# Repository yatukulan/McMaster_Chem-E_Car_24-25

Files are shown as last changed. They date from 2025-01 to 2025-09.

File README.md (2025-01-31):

# McMaster_Chem-E_Car_24-25
The codebase for the McMaster Chem-E Car Team from 2024-2025.

This project uses an Adafruit Feather RP2040 Adalogger microcontroller programmed in the Arduino programming language. The car runs off a chemical reaction and is stopped by a chemical reaction as well. However, the code and the microcontroller are used to start the stopping reaction and stir the mixtures while monitoring it to identify when to stop based on a temperature threshold. It also uses an IMU to keep the car going straight, a servo for starting the stopping reaction, two motor drivers to run the drive motors, and two motors for stirring the reactions. The car's main drive system will be powered from a custom-built alkaline battery while the remaining auxiliary systems are powered from a smaller Li-Po battery.

The major components used are as follows:<br />
2 - N20 100 RPM Motors (for drive system)<br />
2 - N20 1000 RPM Motor (for reaction stirring mechanisms)<br />
2 - SER0039 Servo Motor (for initially mixing reactants)<br />
2 - DRV8847 Motor Drivers<br />
1 - DS18B20 Temperature Sensor (for measuring temperature of braking reaction)<br />
1 - Adafruit 9-DOF Orientation IMU Fusion Breakout (BNO085)<br /> 
1 - Adafruit Feather RP2040 Adalogger Microcontroller<br />
1 - 1200 mAh Li-Po Battery<br />

This repository also contains the custom-made PCB design for the component wiring we are using this year. The design was made using Altium, source files & gerber files are present in this repository.

The main objective of the competition is to design a small car to carry a certain amount of weight a set distance while powering and stopping the vehicle with a chemical reaction. The distance and weight vary each year. The compectition is hosted by the American Institute of Chemical Engineers (AIChE).

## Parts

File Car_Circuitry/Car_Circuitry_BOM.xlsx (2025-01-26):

Comment | Description | Designator | Footprint | LibRef | Quantity | Total | Boards
TPS552892RYQR | Integrated Circuit | BOOST1 | TPS552892RYQR | TPS552892RYQR | 1 | 5 | 5
TPS61023DRLT | Integrated Circuit | BOOST2 | SOTFL50P160X60-6N | TPS61023DRLT | 1 | 5
100 nF | Capacitor | C1, C2 | CAPC2012X95N | CL21B104KBCNNNC | 2 | 10
10 μF | Capacitor | C3, C4, C19 | CAPC2012X140N | CL21B106KOQNNNE | 3 | 15
82 nF | Capacitor | C5 | CAPC1005X55N | GRM155R61A823KA01D | 1 | 5
24 nF | Capacitor | C6 | CAPC2013X94N | 08051C243JAT2A | 1 | 5
4.7 μF | Capacitor | C7 | CAPC1608X80N | C1608X6S1C475K080AC | 1 | 5
56 μF | Capacitor Polarised | C8 | 16SVF82M | 20SVPF56MX | 1 | 5
22 μF | Capacitor | C9, C15, C16, C17 | CAPC3225X270N | GRM32ER61E226KE15K | 4 | 20
100 nF | Capacitor | C10, C11, C12, C18 | CAPC1005X55N | CL05B104KA5NNNC | 4 | 20
27 μF | Capacitor Polarised | C13, C14 | 16SVF82M | 25SVPF27MX | 2 | 10
22 μF | Capacitor | C20, C21 | CAPC3216X180N | CL31B226KPHNNNE | 2 | 10
SSB44-M3_5BT | Schottky Diode | D1 | DIOM5436X244N | SSB44-M3_5BT | 1 | 5
B2B-XH-A(LF)(SN) | CONN HEADER VERT 2POS 2.5MM | DRML, DRMR, PROP, SOL, STMB, STMP, SW | FP-B2B-XH-A_LF_SN-MFG | CMP-2000-05888-3 | 7 | 35
DRV8847PWPR | Integrated Circuit | DRV1, DRV2 | SOP65P640X120-17N | DRV8847PWPR | 2 | 10
4.7 μH | Inductor | L1 | INDPM6664X610N | 74439346047 | 1 | 5
1 μH | Inductor | L2 | 74438357010 | 74438357010 | 1 | 5
Feather RP2040 Adalogger | Adafruit Microcontroller | MCU | 2796 | 2796 | 1 | 5
DMN6075S-7 | MOSFET (N-Channel) | Q1 | SOT96P240X110-3N | DMN6075SQ-7 | 1 | 5
110 mΩ | Resistor | R1, R4 | ERJ6_B_BW_R_LW_CW_D | ERJ-6DSFR11V | 2 | 10
680 mΩ | Resistor | R2, R5 | ERJ6_B_BW_R_LW_CW_D | ERJ-6DQJR68V | 2 | 10
10 kΩ | Resistor | R3, R6, R10 | RESC2012X70N | ERJ-6GEYJ103V | 3 | 15
4.7 kΩ | Resistor | R7 | RESAD1530W60L610D230 | CF1_4C472J | 1 | 5
301 Ω | Resistor | R8 | RESC1005X40N | CRCW0402301RFKED | 1 | 5
49.9 kΩ | Resistor | R9 | ERJ2RKD1004X | ERJ-2RKF4992X | 1 | 5
100 kΩ | Resistor | R11 | ERJ8ENF1000V | ERJ-8ENF1003V | 1 | 5
732 kΩ | Resistor | R12 | ERJ8ENF1000V | ERJ-8ENF7323V | 1 | 5
B3B-XH-A(LF)(SN) | CONN HEADER VERT 3POS 2.5MM | SVOB, SVOP, TMP | FP-B3B-XH-A_LF_SN-MFG | CMP-17439-000014-3 | 3 | 15

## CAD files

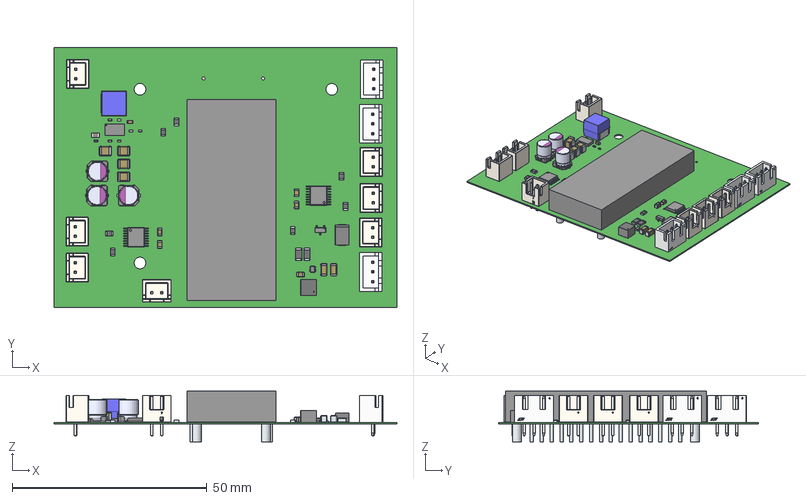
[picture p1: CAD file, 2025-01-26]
Car_Circuitry/Car_Circuitry.step
88.1 x 66.9 x 13.1 mm
solidBody x 10
Terminal x 10
solidTop x 10
FilletPin1 x 2
FilletPin2 x 2
B2B-XH-A x 7
JST Logo adjustable x 7
PinsArrayL
FilletPinR
Pins x 3
Marking x 3
JST Logo x 3
body_SSMC_4030
land_pattern_SSMC_4020 x 2
R7
Leads x 32
PinsArrayLR x 2
ThermalPad x 2
BODY-SOT
PIN1-ID

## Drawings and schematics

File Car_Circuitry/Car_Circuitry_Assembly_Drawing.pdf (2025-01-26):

1

16

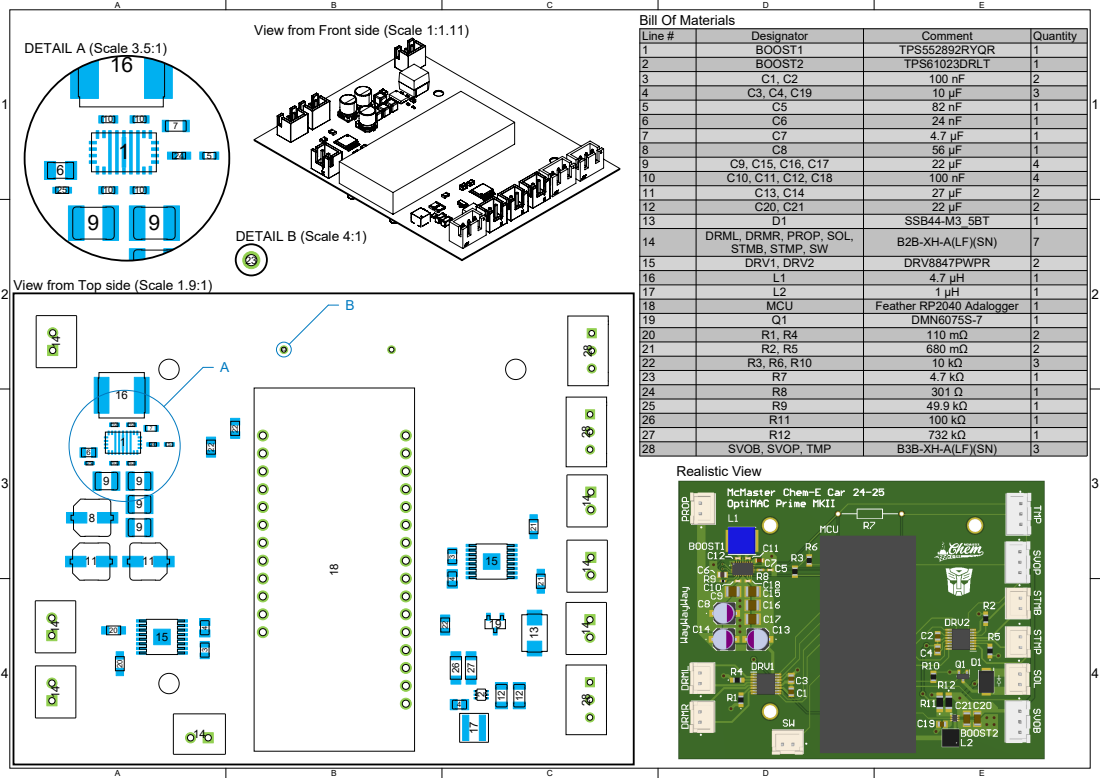
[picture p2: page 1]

View from Front side (Scale 1:1.11)

Line # | Designator | Comment | Quantity
1 | BOOST1 | TPS552892RYQR | 1
2 | BOOST2 | TPS61023DRLT | 1
3 | C1, C2 | 100 nF | 2
4 | C3, C4, C19 | 10 μF | 3
5 | C5 | 82 nF | 1
6 | C6 | 24 nF | 1
7 | C7 | 4.7 μF | 1
8 | C8 | 56 μF | | 1
9 | C9, C15, C16, C17 | 22 μF | | 4
10 | C10, C11, C12, C18 | 100 nF | | 4

12 | C20, C21 | 22 μF | 2
13 | D1 | SSB44-M3_5BT | 1
14 | DRML, DRMR, PROP, SOL, STMB, STMP, SW | B2B-XH-A(LF)(SN) | 7

15 | DRV1, DRV2 | DRV8847PWPR | 2
16 | L1 | 4.7 μH | 1
17 | L2 | 1 μH | 1
18 | MCU | Feather RP2040 Adalogger | 1
19 | Q1 | DMN6075S-7 | 1
20 | R1, R4 | 110 mΩ | 2
21 | R2, R5 | 680 mΩ | 2
22 | R3, R6, R10 | 10 kΩ | 3
23 | R7 | 4.7 kΩ | 1
24 | R8 | 301 Ω | 1
25 | R9 | 49.9 kΩ | 1
26 | R11 | 100 kΩ | 1
27 | R12 | 732 kΩ | 1
28 | SVOB, SVOP, TMP | B3B-XH-A(LF)(SN) | 3

View from Top side (Scale 1.9:1)

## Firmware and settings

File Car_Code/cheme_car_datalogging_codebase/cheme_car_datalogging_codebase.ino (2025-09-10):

// Included libraries
#include <OneWire.h>
// #include <Wire.h>
// #include <Adafruit_BNO08x.h>
#include <DallasTemperature.h>
// #include <PID_v1_bc.h>
#include <Servo.h>
#include <Adafruit_NeoPixel.h>
#include "SdFat.h"

#define NUM_PIXELS 1 // Status LED

// Add Test Fork

// Define drive motor pins
#define LEFT_PWM_1 9
#define LEFT_PWM_2 10
#define RIGHT_PWM_1 12
#define RIGHT_PWM_2 11

// Define the PWM pins for the stir bar motors
#define BRAK_STIR_PWM_1 A3
#define BRAK_STIR_PWM_2 24
#define PROP_STIR_PWM_1 6
#define PROP_STIR_PWM_2 5

// Define servo pins
#define BRAK_SERVO_PWM 13
#define PROP_SERVO_PWM 4

#define BRAK_TEMP_SENS A1 // Pin for the teperature sensor data line

// #define BNO08X_RESET -1 // No reset pin for IMU over I2C, only enabled for SPI

// #define BOOST_I2C 0x75 // This is the address when pin on converter is set to LOW

// Define chip select pin for SD card
#define SD_CS_PIN 23

// Struct for Euler Angles
// struct euler_t
// {
//   float yaw;
//   float pitch;
//   float roll;
// } ypr;

// Create servo objects
Servo brak_servo;
Servo prop_servo;

// Create BNO085 instance
// Adafruit_BNO08x bno08x(BNO08X_RESET);
// sh2_SensorValue_t sensor_value;

OneWire one_wire(BRAK_TEMP_SENS);          // Create a OneWire instance to communicate with the sensor
DallasTemperature temp_sensors(&one_wire); // Pass OneWire reference to Dallas Temperature sensor

Adafruit_NeoPixel pixel(NUM_PIXELS, PIN_NEOPIXEL, NEO_GRB + NEO_KHZ800); // Status LED

// Define files
SdFat sd;
FsFile root;
FsFile next_file;
FsFile data_file;
SdSpiConfig config(SD_CS_PIN, DEDICATED_SPI, SD_SCK_MHZ(16), &SPI1);
String file_name;

bool is_file_new = true; // Checks for new file

// The target yaw angle to keep car straight
// double goal_yaw = 0.0;

// Define IMU variables
// double yaw;            // yaw angle
// double init_yaw = 0.0; // initial yaw angle
// double yaw_diff = 0.0; // yaw angle difference

// Delta temperature
double temp_diff;

// Temperature change threshold
double temp_change;

// Initialize run count for SD card file
int run_count;

// variables to store temperature
double temperature_c; // Current temperature
double init_temp;     // Initial temperature for differential calculation

// KALMAN FILTER variables
double x_temp; // Filtered temperature
double p_temp; // Initial error covariance
// double x_IMU;  // Filtered temperature
// double p_IMU;  // Initial error covariance

// Process noise and measurement noise
double q_temp; // Process noise covariance
double r_temp; // Measurement noise covariance
// double q_IMU;  // Process noise covariance
// double r_IMU;  // Measurement noise covariance

// Keeping track of time
double curr_time = 0.0f;
unsigned long start_time;
// bool first_run = true;

const int data_size = 4; // Number of items to log
double data[data_size];  // Data array
// char data_buf[11];       // Data buffer

// PID Loop variables
// double pid_output; // The output correction from the PID algorithm

// The following numbers need to be adjusted through testing
// double k_p = 1.5;  // Proportional weighting
// double k_i = 0.03; // Integral weighting
// double k_d = 0.3;  // Derivative weighting

// Offsets & speeds for left and right wheel
// int left_offset = 0;
// int right_offset = 0;
int drive_speed = 128;
// int max_offset;

// PID control object; input, output, and goal angle are passed by pointer.
// PID car_pid(&yaw_diff, &pid_output, &goal_yaw, k_p, k_i, k_d, DIRECT);

// Buck boost converter status outputs
// bool buck_boost_short_circuit;
// bool buck_boost_overcurrent;
// bool buck_boost_overvoltage;
// String buck_boost_op_status;

// void init_buck_boost(void)
// {
//   Wire.begin(); // Begin I2C communication

//   // Change internal output voltage to 676.68 mV
//   // Change LSB
//   Wire.beginTransmission(BOOST_I2C);
//   Wire.write(0x00); // Register Address
//   Wire.write(0x5F); // Changed LSB
//   Wire.endTransmission();

//   //  Change MSB
//   Wire.beginTransmission(BOOST_I2C);
//   Wire.write(0x01); // Register Address
//   Wire.write(0x04); // Changed MSB
//   Wire.endTransmission();

//   // Disable current limiter
//   Wire.beginTransmission(BOOST_I2C);
//   Wire.write(0x02); // Register Address
//   Wire.write(0x64); // Changed LSB
//   Wire.endTransmission();

//   // Enable output
//   Wire.beginTransmission(BOOST_I2C);
//   Wire.write(0x06); // Register Address
//   Wire.write(0xA0); // Changed LSB
//   Wire.endTransmission();
// }

// String check_buck_boost_status(void)
// {
//   // Read status register
//   Wire.beginTransmission(BOOST_I2C);
//   Wire.write(0x07);
//   Wire.endTransmission(false);
//   Wire.requestFrom(BOOST_I2C, 1);

//   char status = Wire.read();

//   // Check SCP status
//   if (((status >> 7) & 0x01))
//   {
//     buck_boost_short_circuit = true;
//   }

//   // Check OCP status
//   if (((status >> 6) & 0x01))
//   {
//     buck_boost_overcurrent = true;
//   }

//   // Check OVP status
//   if (((status >> 5) & 0x01))
//   {
//     buck_boost_overvoltage = true;
//   }

//   // Check operating status
//   switch (status << 6)
//   {
//   case 0x00:
//     return "boost";
//   case 0x40:
//     return "buck";
//   case 0x80:
//     return "buck-boost";
//   case 0xC0:
//     return "reserved";
//   default:
//     return "";
//   }
// }

void drive_forward(int speed) // Drive function
{
  digitalWrite(LEFT_PWM_1, HIGH);
  digitalWrite(RIGHT_PWM_2, HIGH);
  // analogWrite(LEFT_PWM_2, speed - left_offset);
  // analogWrite(LEFT_PWM_2, speed);
  digitalWrite(LEFT_PWM_2, LOW);
  // analogWrite(RIGHT_PWM_1, speed - right_offset);
  // analogWrite(RIGHT_PWM_1, speed);
  digitalWrite(RIGHT_PWM_1, LOW);
}

void stop_driving(void) // Stop function
{
  digitalWrite(LEFT_PWM_1, HIGH);
  digitalWrite(RIGHT_PWM_2, HIGH);
  // analogWrite(LEFT_PWM_2, 255);
  digitalWrite(LEFT_PWM_2, HIGH);
  // analogWrite(RIGHT_PWM_1, 255);
  digitalWrite(RIGHT_PWM_1, HIGH);
}

void servo_dump(Servo servo, int angle_us, int delay_ms) // Dump reactants into vessel with servo
{
  // Rotate to specified position
  servo.writeMicroseconds(angle_us);
  delay(500);
  servo.writeMicroseconds(angle_us);

  delay(delay_ms); // Wait specified delay

  // Return to default position
  servo.writeMicroseconds(450);
  delay(500);
  servo.writeMicroseconds(450);
}

void start_stir(int stir_pin_1, int stir_pin_2, int speed) // Start stirring mechanism
{
  digitalWrite(stir_pin_1, LOW);  // For fast decay
  analogWrite(stir_pin_2, speed); // Set motor to speed obtained through testing
}

// void PID_loop(void) // Update motor speeds according to PID algorithm
// {
//   car_pid.Compute(); // Run compute algorithm and updates pid_output

//   if (pid_output < 0)
//   {
//     left_offset = abs(round(pid_output)); // If output needs to be adjusted in positive dir (to the right), increase left wheel speed
//     right_offset = round(pid_output);     // and decrease right wheel speed.
//   }
//   else if (pid_output > 0)
//   {
//     right_offset = abs(round(pid_output)); // If output needs to be adjusted in negative dir (to the left), increase right wheel speed
//     left_offset = -round(pid_output);      // and decrease left wheel speed.
//   }
//   else // Otherwise set both speed offsets to zero if output does not need adjustment.
//   {
//     left_offset = 0;
//     right_offset = 0;
//   }
// }

void kalman_filter(double x_k, double p_k, double q, double r, double input, bool tempTrue) // Kalman filtering algorithm
{
  // Kalman filter prediction
  double x_k_minus = x_k;     // Predicted next state estimate
  double p_k_minus = p_k + q; // Predicted error covariance for the next state

  // Kalman filter update

  /* Kalman gain: calculated based on the predicted error covariance
  and the measurement noise covariance, used to update the
  state estimate (x_k) and error covariance (p_k) */
  double k = p_k_minus / (p_k_minus + r); // Kalman gain

  // Comparison with actual sensor reading
  x_k = x_k_minus + k * (input - x_k_minus); // Updated state estimate
  p_k = (1 - k) * p_k_minus;                 // Updated error covariance

  if (tempTrue) // Update state for temperature sensor or IMU accordingly
  {
    x_temp = x_k;
    p_temp = p_k;
  }
  else
  {
    // x_IMU = x_k;
    // p_IMU = p_k;
  }
}

void printer(bool serial_true, double millis_time, double outputs[data_size]) // Output function
{
  if (serial_true) // Print data to serial or SD card file accordingly in .csv format
  {
    Serial.print(millis_time, 6);

    for (int i = 0; i < data_size; i++)
    {
      Serial.print(",");
      Serial.print(outputs[i], 6);
    }

    Serial.println("");
  }
  else
  {
    data_file.print(millis_time, 6);

    for (int i = 0; i < data_size; i++)
    {
      data_file.print(",");
      data_file.print(outputs[i], 6);
    }

    data_file.println("");
  }
}

// Enable reports for IMU
// void setReports(void)
// {
//   Serial.println("Setting desired reports");
//   if (!bno08x.enableReport(SH2_ARVR_STABILIZED_RV))
//   {
//     Serial.println("Could not enable rotation vector");
//   }
// }

// Convert Quaternion to Euler Angles to get yaw
// void quaternionToEuler(float qr, float qi, float qj, float qk, euler_t *ypr, bool degrees = false)
// {

//   float sqr = sq(qr);
//   float sqi = sq(qi);
//   float sqj = sq(qj);
//   float sqk = sq(qk);

//   ypr->yaw = atan2(2.0 * (qi * qj + qk * qr), (sqi - sqj - sqk + sqr));
//   ypr->pitch = asin(-2.0 * (qi * qk - qj * qr) / (sqi + sqj + sqk + sqr));
//   ypr->roll = atan2(2.0 * (qj * qk + qi * qr), (-sqi - sqj + sqk + sqr));

//   if (degrees)
//   {
//     ypr->yaw *= RAD_TO_DEG;
//     ypr->pitch *= RAD_TO_DEG;
//     ypr->roll *= RAD_TO_DEG;
//   }
// }

// Pointer function
// void quaternionToEulerRV(sh2_RotationVectorWAcc_t *rotational_vector, euler_t *ypr, bool degrees = false)
// {
//   quaternionToEuler(rotational_vector->real, rotational_vector->i, rotational_vector->j, rotational_vector->k, ypr, degrees);
// }

void setup(void) // Setup (executes once)
{
  // Indicate status to be initialized
  pixel.begin();
  pixel.setBrightness(255);
  pixel.show();
  pixel.setPixelColor(0, 255, 0, 0);
  pixel.show();

  // Get time at start
  start_time = millis();

  while (!sd.begin(config))
  {
    delay(1000); // Wait for a second before retrying
  }

  root = sd.open("/", FILE_READ); // Open SD root directory
  run_count = 0;

  while (true)
  {
    next_file = root.openNextFile();

    if (next_file)
    {
      run_count++; // Increment with each existing file
    }
    else
    {
      next_file.close();
      break;
    }
  }

  root.close();

  // Setting to drive motors output mode
  pinMode(LEFT_PWM_1, OUTPUT);
  pinMode(LEFT_PWM_2, OUTPUT);
  pinMode(RIGHT_PWM_1, OUTPUT);
  pinMode(RIGHT_PWM_2, OUTPUT);

  stop_driving(); // Stop driving motors from any residual bootloader code

  // Initialize the stir motor pins as outputs
  pinMode(BRAK_STIR_PWM_1, OUTPUT);
  pinMode(BRAK_STIR_PWM_2, OUTPUT);
  pinMode(PROP_STIR_PWM_1, OUTPUT);
  pinMode(PROP_STIR_PWM_2, OUTPUT);

  // Initialize buck-boost converter status outputs
  // buck_boost_short_circuit = false;
  // buck_boost_overcurrent = false;
  // buck_boost_overvoltage = false;

  // init_buck_boost(); // Initialize buck-boost converter

  // Setting the stir speed
  start_stir(BRAK_STIR_PWM_1, BRAK_STIR_PWM_2, 255);
  start_stir(PROP_STIR_PWM_1, PROP_STIR_PWM_2, 255);

  temp_sensors.begin();                        // Initialize the DS18B20 sensor
  temp_sensors.requestTemperatures();          // Request temperature from all devices on the bus
  init_temp = temp_sensors.getTempCByIndex(0); // Get temperature in Celsius

  // bno08x.begin_I2C();
  // setReports();

  // Poll IMU a few times & wait for initialization value to stabilize
  // for (int i = 0; i < 5; i++)
  // {
  //   bno08x.getSensorEvent(&sensor_value);
  //   quaternionToEulerRV(&sensor_value.un.arvrStabilizedRV, &ypr, true);

  //   init_yaw = ypr.yaw;
  //   yaw = ypr.yaw;
  //   yaw_diff = yaw - init_yaw;

  //   delay(200);
  // }

  // Initialize Kalman filter parameters
  x_temp = init_temp; // Initial state estimate
  p_temp = 0.1;       // Initial error covariance
  q_temp = 0.01;      // Process noise covariance
  r_temp = 0.5;       // Measurement noise covariance
  // x_IMU = yaw_diff;   // Initial state estimate
  // p_IMU = 0.0;        // Initial error covariance
  // q_IMU = 0.01;       // Process noise covariance
  // r_IMU = 5.674;      // Measurement noise covariance

  // Initialize servo to default position
  prop_servo.writeMicroseconds(450);
  prop_servo.attach(PROP_SERVO_PWM, 400, 2600);
  prop_servo.writeMicroseconds(450);
  delay(2000);
  brak_servo.writeMicroseconds(450);
  brak_servo.attach(BRAK_SERVO_PWM, 400, 2600);
  brak_servo.writeMicroseconds(450);
  delay(2000);

  // Dump reactants before starting drive
  servo_dump(prop_servo, 2500, 3000);
  delay(7000);
  servo_dump(brak_servo, 2500, 3000);

  start_time = micros(); // First measurement saved seperately
  curr_time = 0;         // Set current time to zero from start time

  delay(17000);

  // Set max speed offset according to drive speed
  // if (drive_speed < 128)
  // {
  //   max_offset = drive_speed;
  // }
  // else
  // {
  //   max_offset = 255 - drive_speed;
  // }

  // Activate PID
  // car_pid.SetMode(AUTOMATIC);

  // The pid outputs between -51 to 51 depending on how the motors should be adjusted. An output of 0 means no change. (This should be adjusted through testing).
  // car_pid.SetOutputLimits(-max_offset, max_offset);

  pixel.setPixelColor(0, 0, 0, 255); // Indicate setup complete status
  pixel.show();
}

void loop(void) // Loop (main loop)
{
  drive_forward(0); // 100% speed in slow decay mode

  curr_time = (micros() - start_time) / 1000000.0f; // Taken to check time against first measurement

  // buck_boost_op_status = check_buck_boost_status();

  temp_sensors.requestTemperatures();              // Request temperature from all devices on the bus
  temperature_c = temp_sensors.getTempCByIndex(0); // Get temperature in Celsius

  // bno08x.getSensorEvent(&sensor_value);
  // quaternionToEulerRV(&sensor_value.un.arvrStabilizedRV, &ypr, true);

  // yaw = ypr.yaw;
  // yaw_diff = yaw - init_yaw;

  // Update kalman filters
  kalman_filter(x_temp, p_temp, q_temp, r_temp, temperature_c, true);
  // kalman_filter(x_IMU, p_IMU, q_IMU, r_IMU, yaw_diff, false);

  temp_diff = x_temp - init_temp;
  temp_change = double(0.185) * curr_time - 4.5f; // Calculate temperature change

  // Update data array
  // dtostrf(temperature_c, 3, 6, data_buf);
  data[0] = temperature_c;
  // dtostrf(x_temp, 3, 6, data_buf);
  data[1] = x_temp;
  // dtostrf(yaw_diff, 3, 6, data_buf);
  data[2] = temp_diff;
  // dtostrf(x_IMU, 3, 6, data_buf);
  data[3] = temp_change;
  // data[4] = String(buck_boost_short_circuit);
  // data[5] = String(buck_boost_overcurrent);
  // data[6] = String(buck_boost_overvoltage);
  // data[7] = buck_boost_op_status;

  // Open csv file
  file_name = "Run_" + String(run_count) + ".csv";
  data_file = sd.open(file_name, FILE_WRITE);

  // Write to csv file
  if (data_file)
  {
    // Write file header
    if (is_file_new)
    {
      data_file.println("Time (s),Raw Temperature (deg C),Filtered Temperature (deg C),Delta T (deg C),Temperature Line (deg C)");
      is_file_new = false;
    }

    printer(false, curr_time, data); // Write variable data to the file in CSV format

    data_file.close();
  }

  // printer(true, curr_time, data); // Write variable data to serial in CSV format

  Serial.print(curr_time);
  Serial.print(",");
  Serial.print(temperature_c);
  Serial.print(",");
  Serial.print(x_temp);
  Serial.print(",");
  Serial.print(temp_diff);
  Serial.print(",");
  Serial.println(temp_change);

  // Update PID model
  // PID_loop();

  if (temp_diff <= temp_change)
  {
    // Stop driving
    stop_driving();

    // Wire.end(); // End I2C comms with buck-boost converter

    // Indicate status to be finished
    pixel.setPixelColor(0, 0, 255, 0);
    pixel.show();

    while (1)
      ; // Do nothing for remainder of uptime
  }
}

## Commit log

2024-11-13 initial commit using last year's codebase
    [Car_Circuitry.PcbDoc, Car_Circuitry.PrjPcb, Car_Circuitry.SchDoc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]
2024-11-15 refined repo for this year & removed some vestiges from last year's code.
    [Car_Circuitry.PcbDoc, Car_Circuitry.SchDoc]
2024-11-24 Updated code for second servo on pin 4
2024-11-24 Added code for conductivity probe
2024-11-30 Removed servo 2 changes
2024-12-01 Removed temperature change code
2025-01-10 Revert "Update Car_Circuitry.PcbDoc"
    This reverts commit e4d685bfff2f7684db28988fec14f9bf25b0303c.
    [Car_Circuitry.PcbDoc]
2025-01-10 Fixed Conductivity Connector
    Reverted the Temp Connector and used your footprint for the Conductivity Connector, but still doesn't have the IMU because it was causing some error, I'm gonna try and get it to work but I wanted to commit this first
    [Car_Circuitry.PcbDoc, Car_Circuitry.SchDoc]
2025-01-11 Conductivity Sensor
    Fixed the Conductivity Sensor and added back the IMU. Shout out to Aithihya for helping and suffering with me.
    [Car_Circuitry.PcbDoc, Car_Circuitry.PrjPcb, Car_Circuitry.SchDoc]
2025-01-11 Moved Text on PCB
    Moved text slightly to avoid overlap
    [Car_Circuitry.PcbDoc]
2025-01-17 A0 to A02
    Changed conductivity sensor pin on microcontroller from A0 to A2 as requested
    [Car_Circuitry.PcbDoc, Car_Circuitry.SchDoc]
2025-01-19 minor trace routing & silkscreen changes + motor driver refresh
    [Car_Circuitry.PcbDoc, Car_Circuitry.PrjPcb, Car_Circuitry.SchDoc]
2025-01-21 minor changes
    [Car_Circuitry.PcbDoc, Car_Circuitry.SchDoc]
2025-01-21 Merge pull request #2 from ShyavanS/Tarnjots
    removed IMU
    [Car_Circuitry.PcbDoc, Car_Circuitry.SchDoc]
2025-01-21 Merge pull request #5 from ShyavanS/aaryoncircuit
    added solenoid port, beefed up traces.
    [Car_Circuitry.PcbDoc, Car_Circuitry.PrjPcb, Car_Circuitry.SchDoc]
2025-01-21 edit via placement
    [Car_Circuitry.PcbDoc]
2025-01-22 Added finishing touches & re-did power systems.
    Updated boost converter to buck-boost with I2C, made all power traces thicker, added aesthetics.
    [Car_Circuitry.PrjPcb, Car_Circuitry.SchDoc, Car_Circuitry.step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]
2025-01-22 added more vias & moved optimus prime.
    [Car_Circuitry.step]
2025-01-24 Replaced conductivity probe port with backup servo port. Updated pin.
    [Car_Circuitry.SchDoc, Car_Circuitry.step, Car_Circuitry_BOM.xlsx]
2025-01-25 fixed major wiring bug with solenoid.
    [Car_Circuitry.SchDoc, Car_Circuitry.step]
2025-01-25 update bom & things
    [Car_Circuitry.SchDoc, Car_Circuitry.step, Car_Circuitry_BOM.xlsx]
2025-01-26 fixed messed up inductor & updated bom
    [Car_Circuitry.PrjPcb, Car_Circuitry.SchDoc, Car_Circuitry.step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]
2025-01-26 update assembly drawing
    [Car_Circuitry.PrjPcb, Car_Circuitry.SchDoc, Car_Circuitry.step]
2025-01-29 Removed conductivity probe code, added temp sensor code
2025-01-31 made updates for this year's circuitry setup.
2025-02-05 detatch servos
2025-02-13 updated code- with IMU and library-based PID code based on testing and Tarnjot's sample code.
2025-02-20 forgot reset pin for IMU
2025-09-06 added steering daughterboard for nationals & compile mask for multiboard project.
    [Car_Circuitry.PrjPcb, Car_Circuitry.SchDoc, Steering_Daughterboard.PcbDoc]
2025-09-06 saved project
    [Car_Circuitry.PrjPcb]
2025-09-06 cutout for switch
    [Steering_Daughterboard.PcbDoc]
